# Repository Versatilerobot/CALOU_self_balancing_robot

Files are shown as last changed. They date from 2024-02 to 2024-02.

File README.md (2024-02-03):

# CALOU_self_balancing_robot
CALOU is an open source two-wheels inverted pendulum controlled by Bluetooth through a smartphone.

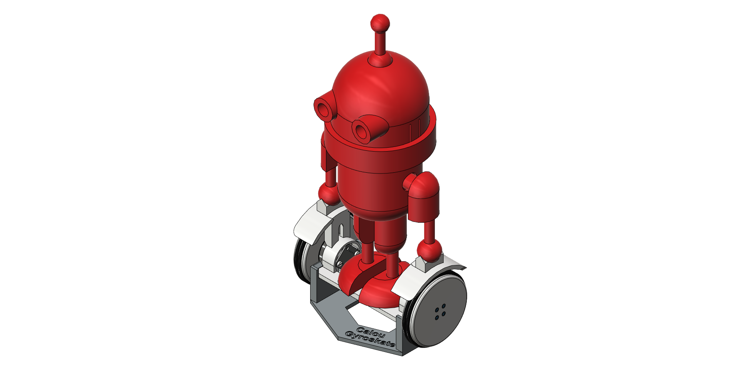
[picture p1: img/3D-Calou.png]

It is a personal project entirely 3D print and powered by two RC Brushless BR2804-100T Gimbal Motor and a 2-axis Brushless Gimbal Controller BGC3.1 MOSFET card in a close loop with angle magnetic encoders. Those parts need some modification &/o adaptation to be assembled. The Controller with the IMU and Bluetooth module HC-05 are located into the head while the Body holds in the center a 500mA – 11.1V – 30C LiPo battery with a switch. The arms and legs of the robot serve as wire guide for motors and encoders.

The program was adapted from an application example of [SimpleFOCproject](https://github.com/simplefoc) : Arduino library implementing a Field Oriented Control (FOC) algorithm for BLDC and Stepper motors: [Arduino-FOC-balancer](https://github.com/simplefoc/Arduino-FOC-balancer)

CALOU is the mascot of the French Robotic Association [Caliban](https://www.facebook.com/AssoCaliban)

It can be controlled through a smartphone by using a remote Bluetooth app and simple commands.   
I hope you will enjoy building this robot and have fun seeing it moving and stabilize and blinking its antenna.

# Assembly Instruction Manual

Assembly instructions have been written in English and French with illustrations to help you in the process step-by-step, making it easier for users to understand and follow:  
[CALOU - self-balancing robot_EN](/CALOU%20-%20self-balancing%20robot_EN.pdf)  
[CALOU - robot en gyroskate_FR](/CALOU%20-%20robot%20en%20gyroskate_FR.pdf)  

The main chapters are:  
Mechanical parts manufacturing; Electronic adaptations and wiring; The assembly steps of the robot; The programming, setting and tests; The starting procedure

A bill of material is also included: [BOM CALOU-GYROSKATE](/BOM%20CALOU-GYROSKATE.pdf)  
And all the STL files for the 3D printing: [3D_STL](/3D_STL)

As a reminder, it is given as is. The author gives no warranty and accepts no responsibility or liability for the accuracy or completeness of the information and materials contained in these instruction manuals.  

# CALOU on YouTube
[CALOU demo](https://youtu.be/TESaMDyrZCY?si=MoILjAsdVkf6BUT1)

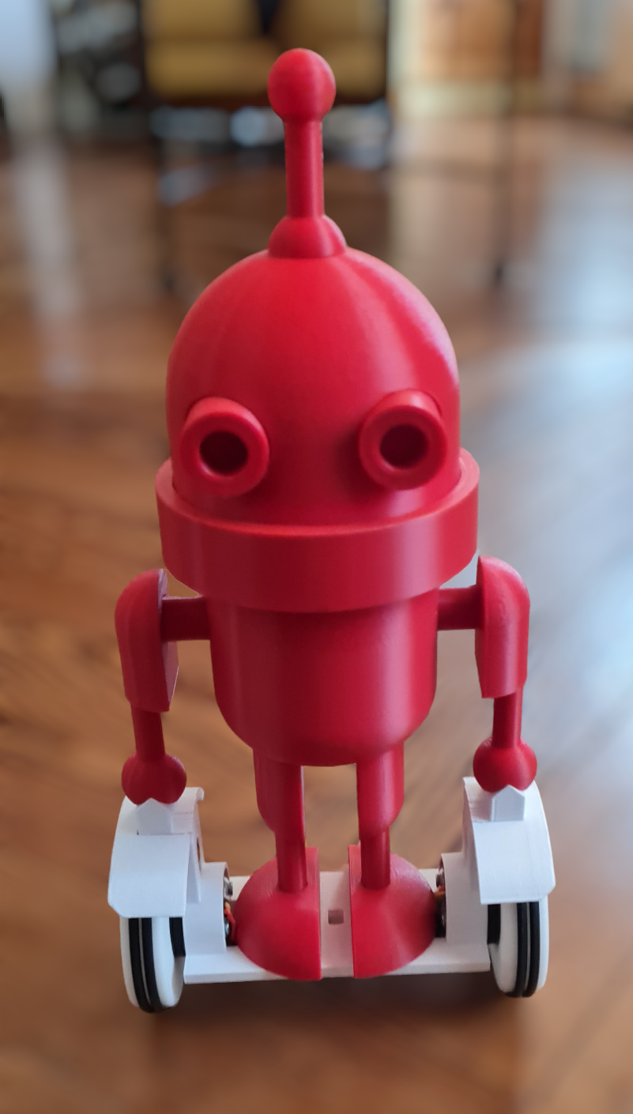
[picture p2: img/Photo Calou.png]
[](https://youtu.be/TESaMDyrZCY?si=MoILjAsdVkf6BUT1)

# Presentation - Apérobot 0x92 - 13th Dec 2023
[Apérobot 0x92 : Guy nous présente CALOU](https://youtu.be/fIwBQCcEI_Y?si=7qKZwHnpSAFOepEM)

Apérobot 0x92 : Guy nous présente CALOU (https://youtu.be/fIwBQCcEI_Y?si=7qKZwHnpSAFOepEM)

# Author

Guy FEUILLOLEY
https://www.facebook.com/versat.ilerobot

# MIT License
Permission is hereby granted, free of charge, to any person obtaining a copy of this software and associated documentation files (the "Software"), to deal in the Software without restriction, including without limitation the rights to use, copy, modify, merge, publish, distribute, sublicense, and/or sell copies of the Software, and to permit persons to whom the Software is furnished to do so, subject to the following conditions:

The above copyright notice and this permission notice shall be included in all copies or substantial portions of the Software.

THE SOFTWARE IS PROVIDED "AS IS", WITHOUT WARRANTY OF ANY KIND, EXPRESS OR
IMPLIED, INCLUDING BUT NOT LIMITED TO THE WARRANTIES OF MERCHANTABILITY, FITNESS FOR A PARTICULAR PURPOSE AND NONINFRINGEMENT. IN NO EVENT SHALL THE
AUTHORS OR COPYRIGHT HOLDERS BE LIABLE FOR ANY CLAIM, DAMAGES OR OTHER LIABILITY, WHETHER IN AN ACTION OF CONTRACT, TORT OR OTHERWISE, ARISING FROM, OUT OF OR IN CONNECTION WITH THE SOFTWARE OR THE USE OR OTHER DEALINGS IN THE SOFTWARE.

# Copyright
Copyright (c) 2024 Versatilerobot

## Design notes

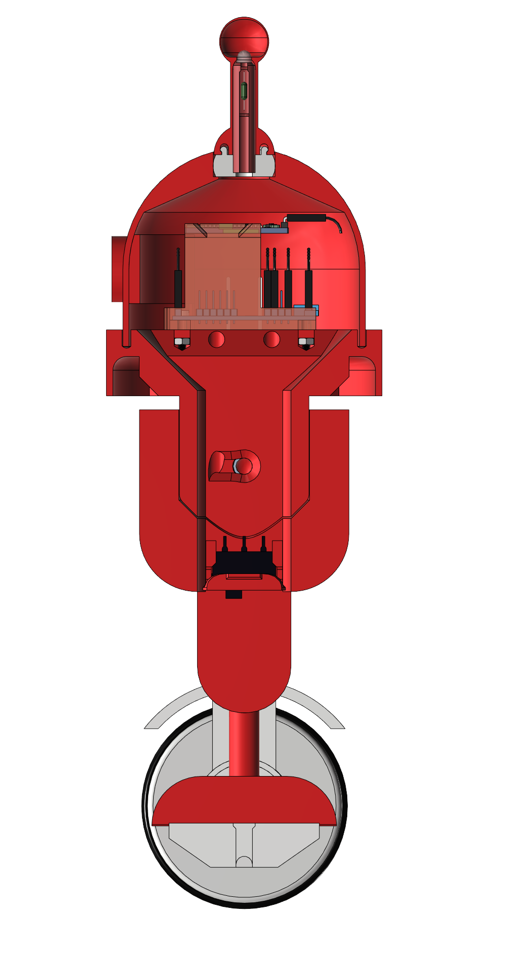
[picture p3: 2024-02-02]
img/CoupeProfil-Calou.png

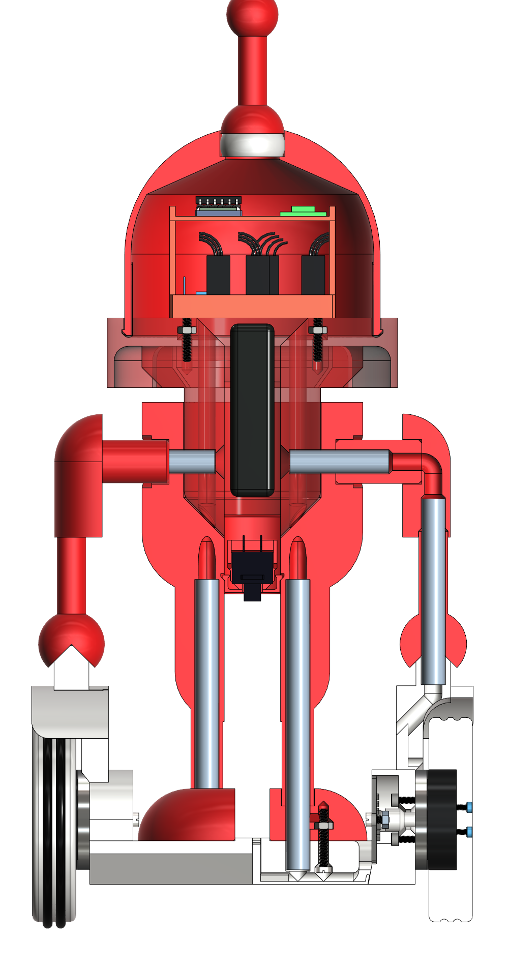
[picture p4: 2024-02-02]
img/CoupeFace-Calou.png

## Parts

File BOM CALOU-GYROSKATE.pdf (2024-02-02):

GF | BOM CALOU-GYROSKATE.xlsx | 02/02/2024

Electronic
componants

Price Per
Parcell €

Quantity
per Parcell

Quantity
needed

Price per
Unit €

Price per
Kit €
| | | | | | Notes | Examples
Moteurs 2804 100KV | 19,34 | 2 | 2 | 9,67 | 19,34 | Moteurs brushless de nacelle de drones | 2pcs/lot RC Brushless Gimbal Motor 2804 100KV For Gopro CNC Digital Camera (https://fr.aliexpress.com/item/32960476136.html)
Contrôleur de cardan sans balais à 2
axes, avec capteur gyro 6050 | 14,73 | 1 | 1 | 14,73 | 14,73 | BGC 3.1 MOS Courant de crête: 10A (à flasher avec bootloader
| | | | | | arduino) - Taille: 5*5cm | 2-axis BGC 3.1 Brushless Gimbal Controller/PTZ Controller motor Driver with 6050
| | | | | | | Sensor for FPV Multirotor (https://fr.aliexpress.com/item/32458535720.html)
Module Capteur d'Angle Magnétique | 1,23 | 1 | 2 | 1,23 | 2,46 | AS5600 - 12 Bits - avec aimant rond 4mm (Voir explication des
| | | | | | modifications à apporter au module 3,3V pour fonctionner en 5V) | TZT AS5600 magnetic encoder angle measurement sensor module 12bit high precision
| | | | | | | For aduino (https://fr.aliexpress.com/item/4000963821667.html)
Module Bluetooth HC-05 | 3,32 | 1 | 1 | 3,32 | 3,32 | Pour le contrôle par smartphone | HC-05 Master-Slave 6Pin, Integrated Bluetooth Serial Pass-Through Module, Wireless
| | | | | | | Serial for Arduino (https://fr.aliexpress.com/item/1005002082974256.html?curPageLogUid=oHJst9pOuJUH)
Accu LiPo 500mAh - 11,1v | 10,99 | 1 | 1 | 10,99 | 10,99 | Dimensions L x l x H = 58 x 32 x16 mm Poids avec câbles = 45g
| | | | | | Fiche d'équilibrage système = XH Fiche de courant système = BEC | Accu LiPo Extron X2 500 - 11,1v (30C - 60C) - Extron (https://www.miniplanes.fr/accu-lipo-extron-x2-500-111v-30c-60c-extron-x6403-p-508804.html)
Super Bright White LED | 0,49 | 1 | 1 | 0,49 | 0,49 | 5mm Super Bright White LED - 3 to 3,2V 20mA | Clear DIP LED Straw Hat (https://www.aliexpress.com/item/1005004635288313.html?curPageLogUid=oHyn5ukkpp4J)
Resistor | 0,12 | 1 | 1 | 0,12 | 0,12 | 1/4W 100Ω (100R) 1% | 100PCS 1/4W 100Ω 1% Metal Film Resistor (https://www.aliexpress.com/item/1005004525936064.html?curPageLogUid=Or2YflaCUnfN)
Extensions de Câble Servos 50cm | 10,99 | 10 | 6 | 1,10 | 6,59 | 3Pin - JR Style - Mâle à Femelle - Câble 22AWG | 10 pcs 50 cm JR Style Servo Extension Câbles (https://www.amazon.fr/dp/B08727C78V?ref=ppx_yo2ov_dt_b_product_details&th=1)
ON-OFF Rocker Switch | 5,09 | 10 | 1 | 0,51 | 0,51 | Black 6Pin ON-OFF - 10A 125V | SPST ON OFF Rocker Position Switch 21*15mm (https://www.aliexpress.com/item/1005006124139215.html)
10cm F to F jumper wires | 0,71 | 1 | 1 | 0,71 | 0,71 | 2.54mm Dupont Line 10cm 40Pin | Female Jumper Wire Dupont Cable DIY KIT (https://www.aliexpress.com/item/32481623557.html?curPageLogUid=Ydw5XZJNEJ00)
1x40 breakable Pin Header | 0,69 | 10 | 1 | 0,07 | 0,07 | Single Row Male 2.54mm Breakable Pin Header Connector Strip | 1x40 Single Row Male 2.54mm Breakable Pin Header Connector Strip (https://www.aliexpress.com/item/4000857385112.html?curPageLogUid=hJ3DWje0BWu6)
Tubes 100mm | 15,59 | 10 | 4 | 1,56 | 6,24 | Tube Droit 8x6mm - Aluminum | 10 Pièces en Aluminium Tube (https://www.amazon.fr/dp/B0BQGZ86W7?psc=1&ref=ppx_yo2ov_dt_b_product_details)
Joints Toriques 75mm | 11,25 | 5 | 4 | 2,25 | 9,00 | 75x68x3,5mm - Nitrile Caoutchouc | Nitrile Caoutchouc Joints Toriques 75mm OD 68mm ID 3.5mm (https://www.amazon.fr/dp/B07JYFP3N5?ref=ppx_yo2ov_dt_b_product_details&th=1)
Vis M2.5x8mm | 5,5 | 50 | 8 | 0,11 | 0,88 | Tête cylindrique - DIN 912 - Acier Inoxydable A2 | 50 Boulons - Tête cylindrique - M2.5x8mm (https://www.amazon.fr/dp/B072MJTMK6?ref=ppx_yo2ov_dt_b_product_details&th=1)
Vis M3x20mm | 13,88 | 20 | 6 | 0,69 | 4,16 | acier inoxydable 304 - tête cylindrique fendue | 20 boulons à tête cylindrique fendue M3 x 20 mm (https://www.amazon.fr/sourcing-map-inoxydable-boulons-cylindrique/dp/B0C143GYQM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)
Vis M3x8mm | 8,78 | 20 | 4 | 0,44 | 1,76 | Tête fraisée - DIN 965 Phillips | 20 vis à tête fraisée M3 x 8 mm en acier inoxydable (https://www.amazon.fr/SECCARO-frais%C3%A9e-inoxydable-Phillips-Filetage/dp/B0CKTK37C4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)
Écrou Hexagonal M3 | 6,99 | 40 | 10 | 0,17 | 1,75 | Acier Inoxydable | 40 Pièces M3 Écrou en Acier Inoxydable (https://www.amazon.fr/Pi%C3%A8ces-Blocage-Inoxydable-Hexagonal-%C3%89crous/dp/B0BDDPQJ9L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)
| | | | | 83,12
3D parts raw material | Price
| €/Kg | Weight
| | g | Quantity
| | | needed | Price Per
| | | | Unit € | Price per
| | | | | kit € | Notes
| | | | | | A titre indicatif seulement - Imprimante Flsun FQQ Pro | Examples
Antenne | 25 | 4 | 1 | 0,10 | 0,10 | 1,25m PLA Rouge 0h24 min | SUNLU Meta Filament PLA 1,75 mm ROUGE (https://www.amazon.fr/dp/B0B24Y84LN/ref=twister_B0B87C7YH4?_encoding=UTF8&th=1)
AvBras | 25 | 4 | 2 | 0,10 | 0,20 | 2,98m PLA Rouge 0h32 min
AxeAimant | 25 | 1 | 2 | 0,03 | 0,05 | 0,23m PLA Rouge 0h16 min
Base | 25 | 38 | 1 | 0,95 | 0,95 | 12,9m PLA Gris 2h47 min | SUNLU Meta Filament PLA 1,75 mm GRIS (https://www.amazon.fr/dp/B0B24W9WLL/ref=twister_B0B87C7YH4?_encoding=UTF8&psc=1)
Bras | 25 | 4 | 2 | 0,10 | 0,20 | 2,92m PLA Rouge 0h48 min
CacheFils | 25 | 1 | 1 | 0,03 | 0,03 | 0,45m PLA Blanc 0h10 min
CaleLedAntenne | 25 | 1 | 1 | 0,03 | 0,03 | 0,46m PLA Rouge 0h16 min
CorpsBas-V2 | 25 | 121 | 1 | 3,03 | 3,03 | 40,56m PLA Rouge 7h10 min
CorpsHaut | 25 | 111 | 1 | 2,78 | 2,78 | 37,16m PLA Rouge 6h34 min
Epaule | 25 | 11 | 2 | 0,28 | 0,55 | 3,57m PLA Rouge 1h22 min
GardeBoue | 25 | 7 | 2 | 0,18 | 0,35 | 2,46m PLA Blanc 0h30 min
GyroskateCorps | 25 | 65 | 1 | 1,63 | 1,63 | 21,71m PLA Blanc 4h02 min
JointLed | 25 | 3 | 1 | 0,08 | 0,08 | 0,89m TPU Blanc 0h10 min | ERYONE TPU Filament 1.75mm (https://www.amazon.fr/ERYONE-Filament-1-75mm-Drucker-0-05mm/dp/B07WDF31WP?hvadid=411298501561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)
Pied | 25 | 14 | 2 | 0,35 | 0,70 | 9,44m PLA Rouge 0h48 min
Roue | 25 | 27 | 2 | 0,68 | 1,35 | 17,94m TPU Blanc 3h04 min | ERYONE TPU Filament 1.75mm (https://www.amazon.fr/ERYONE-Filament-1-75mm-Drucker-0-05mm/dp/B07WDF31WP?hvadid=411298501561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)
SupportBGCboard | 25 | 8 | 1 | 0,20 | 0,20 | 2,83m PLA Rouge 0h58 min
SupportIMU&BLE | 25 | 3 | 1 | 0,08 | 0,08 | 1,00m PLA Rouge 0h17 min
Tête | 25 | 57 | 1 | 1,43 | 1,43 | 19,00m PLA Rouge 3h48 min
TrappeSwitch-V2 | 25 | 3 | 1 | 0,08 | 0,08 | 0,86m PLA Rouge 0h17 min
Yeux | 25 | 21 | 1 | 0,53 | 0,53 | 7,00m PLA Rouge 1h27 min
| | 504 | 27 | | 14,30
3D parts printing electricity | Price
| €/kWh | 3D printer
| | Power W | Quantity
| | | needed h | 3D printer
| | | | price kWh | Price per
| | | | | kit € | Notes
| | | | | | A titre indicatif seulement - Imprimante Flsun FQQ Pro
| 0,21 | 150 | 35,7 | 0,03 | 1,12
Total | | | | | 98,54

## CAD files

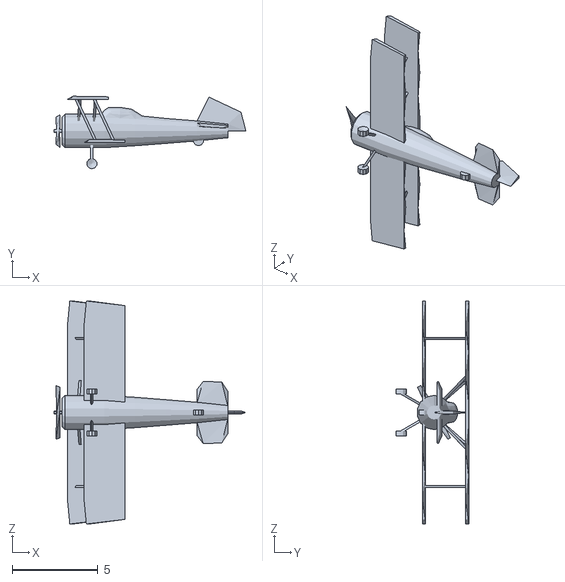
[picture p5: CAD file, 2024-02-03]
Calou_Gyroskate/src/MPU6050/Examples/MPU6050_DMP6_using_DMP_V6.12/MPUplane/data/biplane.obj
11.2 x 4.23 x 13.0

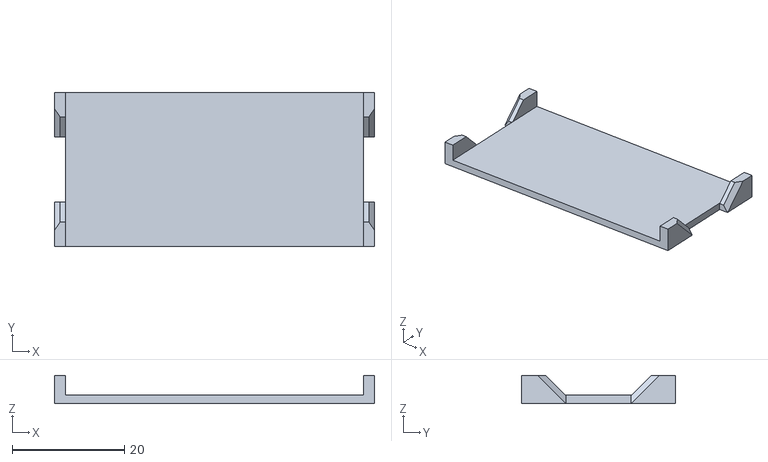
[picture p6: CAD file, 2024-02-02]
3D_STL/SupportIMU&BLE.stl
57.0 x 27.5 x 5.00

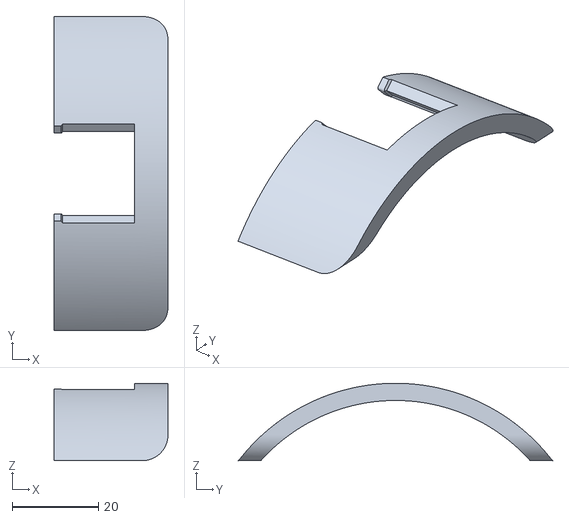
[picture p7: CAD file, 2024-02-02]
3D_STL/GardeBoue.stl
26.5 x 73.0 x 18.0

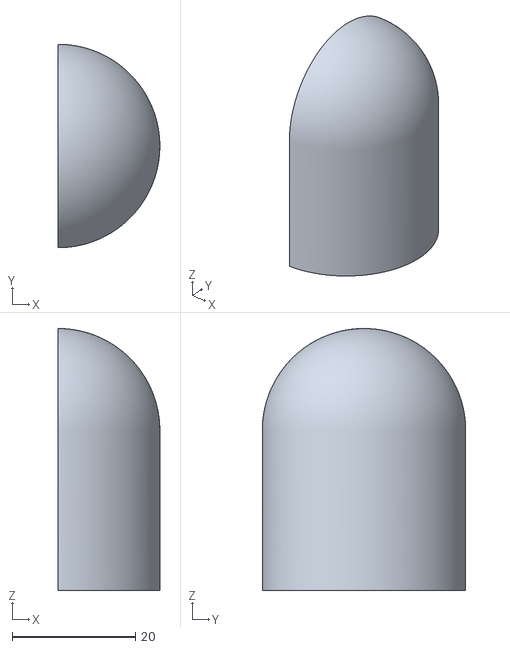
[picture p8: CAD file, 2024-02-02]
3D_STL/Epaule.stl
16.5 x 33.0 x 42.5

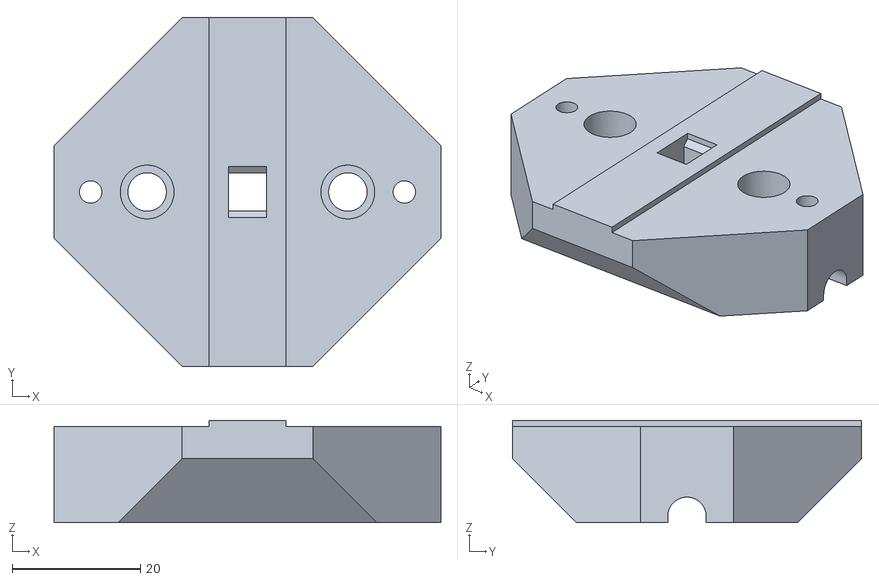
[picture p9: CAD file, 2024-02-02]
3D_STL/FootSpacer.stl
60.4 x 54.5 x 16.0

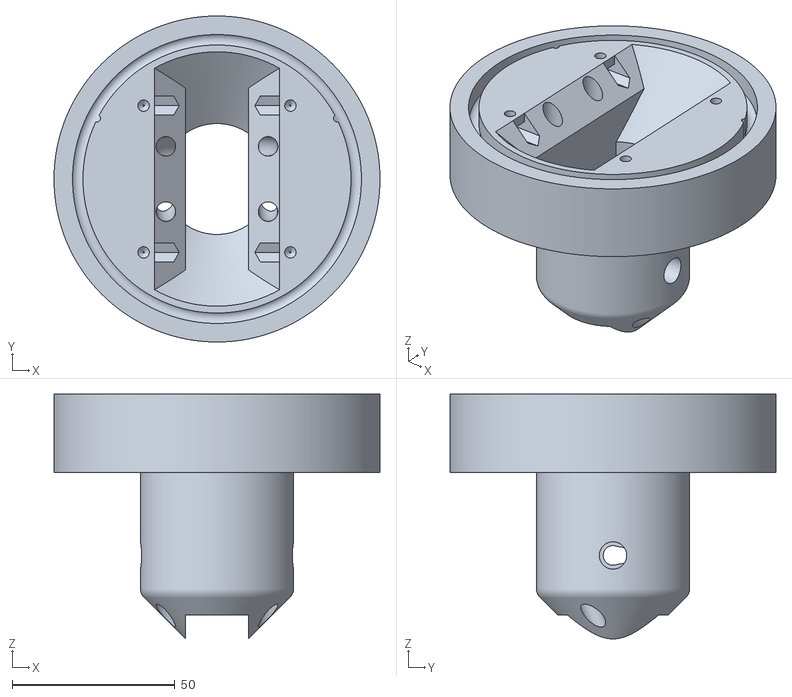
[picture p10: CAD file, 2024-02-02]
3D_STL/CorpsHaut.stl
100.0 x 100.0 x 75.1

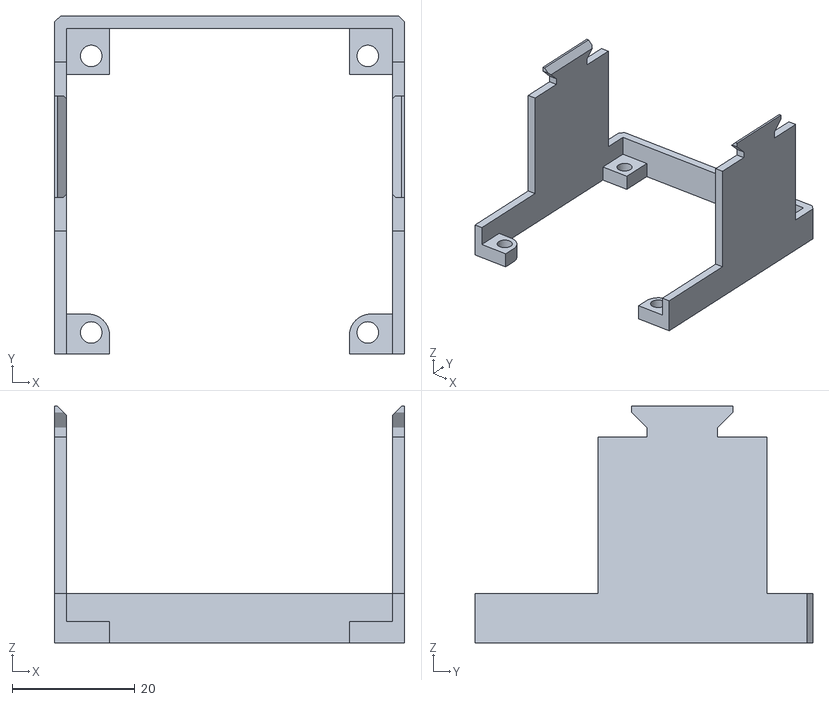
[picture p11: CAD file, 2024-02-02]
3D_STL/SupportBGCboard.stl
57.0 x 55.0 x 38.5

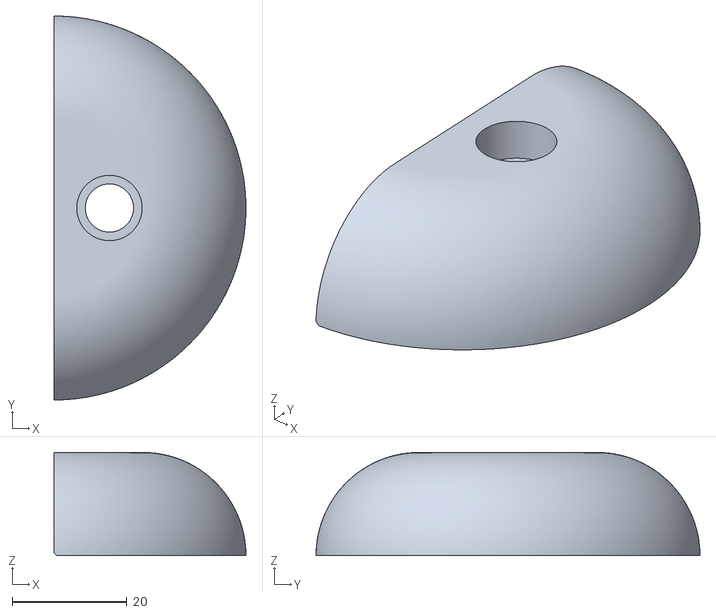
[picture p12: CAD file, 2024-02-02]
3D_STL/Pied.stl
33.5 x 67.0 x 18.0

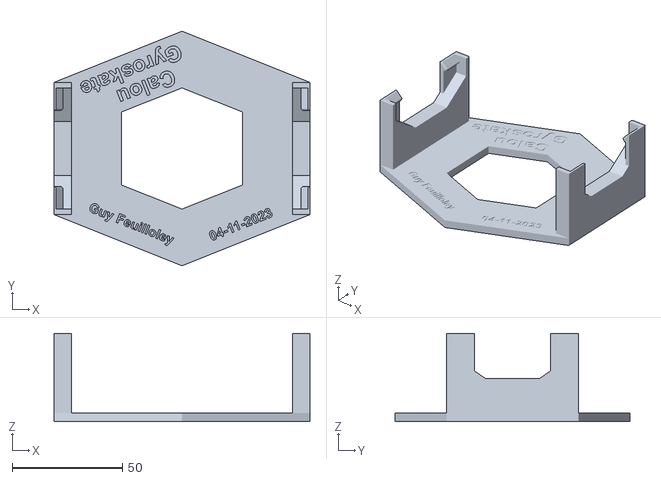
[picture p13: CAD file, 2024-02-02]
3D_STL/Base.stl
116.1 x 106.4 x 40.0

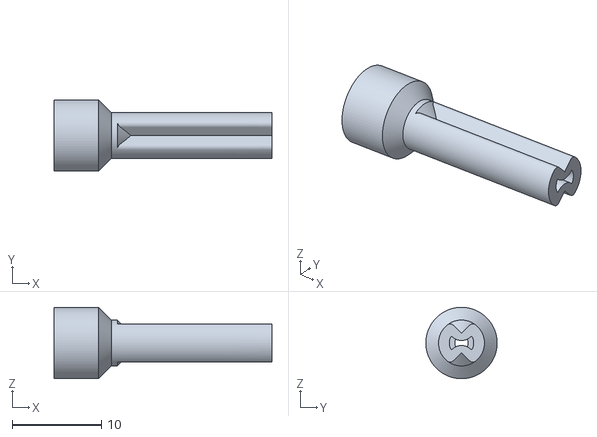
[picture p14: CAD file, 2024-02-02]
3D_STL/AxeAimant.stl
24.4 x 8.00 x 8.00

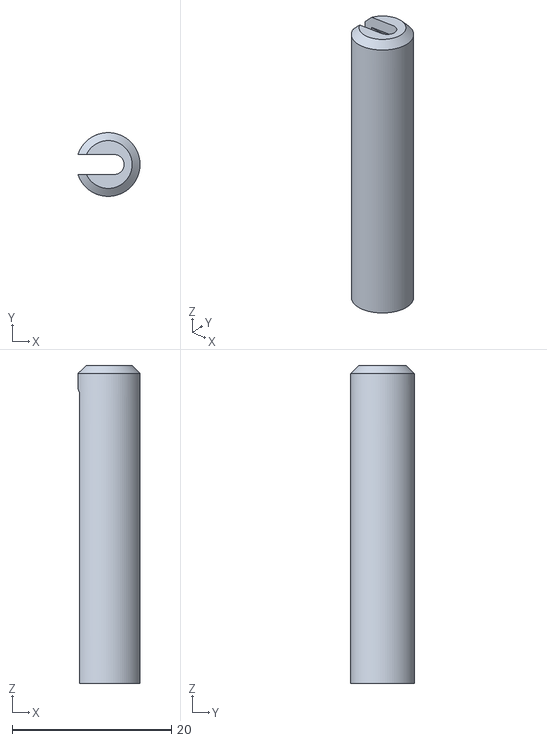
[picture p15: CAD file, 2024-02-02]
3D_STL/CaleLedAntenne.stl
7.80 x 8.00 x 39.9

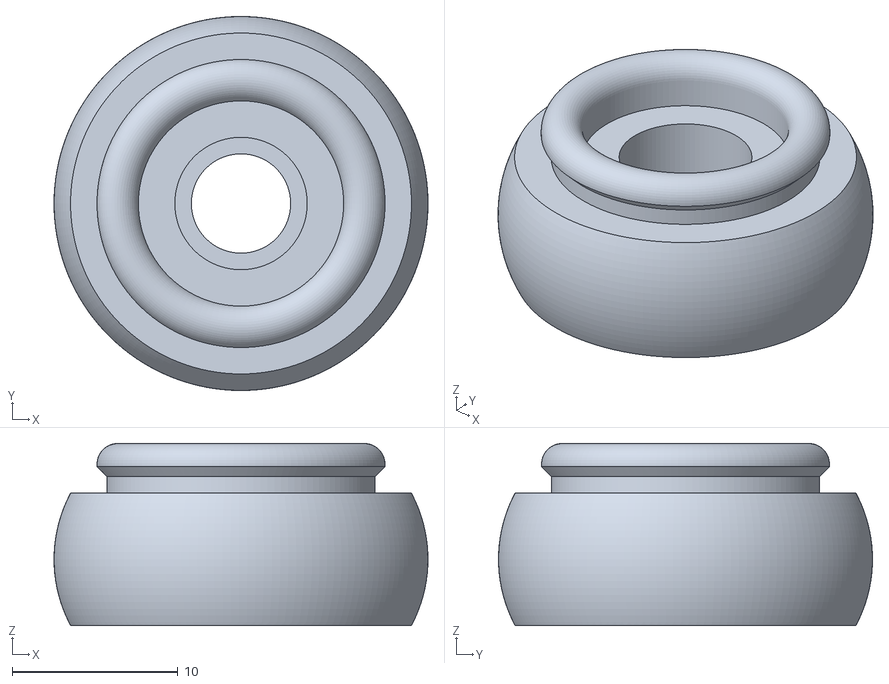
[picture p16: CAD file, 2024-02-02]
3D_STL/JointLed.stl
22.6 x 22.6 x 11.0

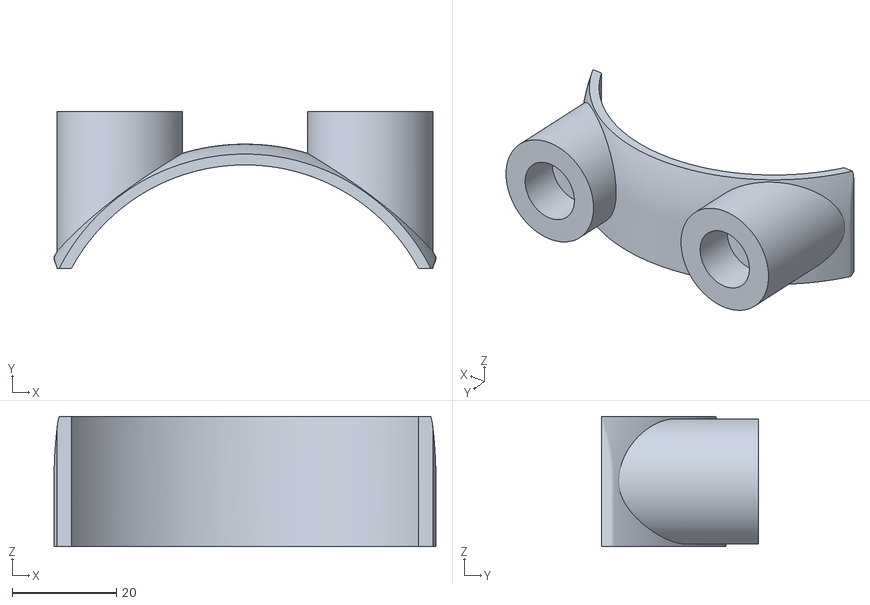
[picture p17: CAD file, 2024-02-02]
3D_STL/Yeux.stl
73.2 x 30.0 x 25.0

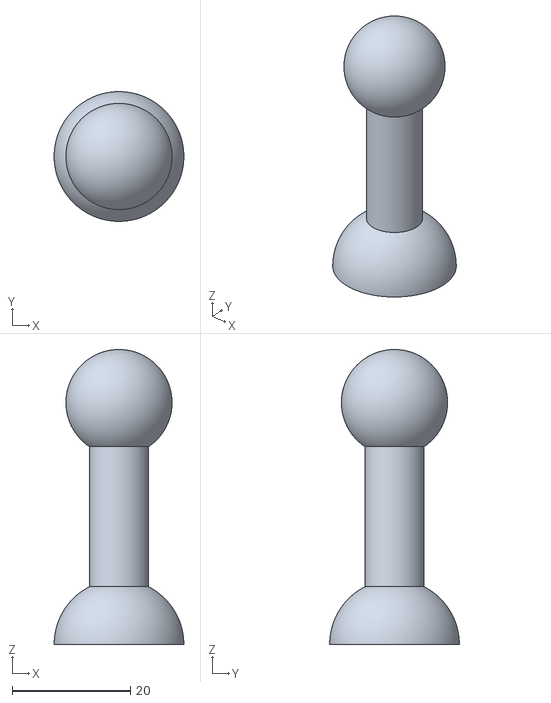
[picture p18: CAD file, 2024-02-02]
3D_STL/Antenne.stl
22.0 x 22.0 x 50.0

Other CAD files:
3D_STL/TrappeSwitch-V3.stl
3D_STL/AvBras.stl
3D_STL/CacheFils.stl
3D_STL/Roue.stl
3D_STL/Bras.stl
3D_STL/GyroskateCorps.stl
3D_STL/TrappeSwitch-V2.stl
3D_STL/Tête.stl

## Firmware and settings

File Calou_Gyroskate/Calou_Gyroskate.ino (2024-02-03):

/* Calou_Gyroskate
 * This is a sketch for a two wheel balancing robot done for a BGC 3.1 Brushless Gimbal Controller with gimbal BLDC motors and SimpleFOClibrary. 
 * It was derived from the application example done for a STM32 Nucleo-64 board you can find on the github "SimpleFOCproject": Arduino SimpleFOCBalancer
 https://docs.simplefoc.com
 https://github.com/simplefoc/Arduino-FOC-balancer
 */

#include "imu_helpers.h"
#include "src/SimpleFOC.h" // ver. 1.61

//// create motor and sensor instances
//BLDCMotor motorL = BLDCMotor(3, 5, 6, 7); // pins + pole pairs
//MagneticSensorAnalog sensorL = MagneticSensorAnalog(A0, 14, 1020);
//
//BLDCMotor motorR = BLDCMotor(9, 10, 11, 7); // pins + pole pairs
//MagneticSensorAnalog sensorR = MagneticSensorAnalog(A1, 14, 1020);

//magnetic sensor instance
MagneticSensorAnalog sensorL = MagneticSensorAnalog(A1, 14, 1020);
MagneticSensorAnalog sensorR = MagneticSensorAnalog(A0, 14, 1020);
// motor instance
BLDCMotor motorL = BLDCMotor(9, 10, 11, 7); // pins + pole pairs
BLDCMotor motorR = BLDCMotor(3, 5, 6, 7); // pins + pole pairs

// control algorithm parameters
// stabilisation pid
PIDController pid_stb{.P = 50, .I = 90, .D = 2, .ramp = 100000, .limit = 10};
// velocity pid
PIDController pid_vel{.P = 0.015, .I = 0.01, .D = 0, .ramp = 2000, .limit = _PI / 10};
// velocity control filtering
LowPassFilter lpf_pitch_cmd{.Tf = 0.35};
// low pass filters for user commands - throttle and steering
LowPassFilter lpf_throttle{.Tf = 0.4};
LowPassFilter lpf_steering{.Tf = 0.01};

// Bluetooth variables
int state = 1;           // stabilization enabling
float steering = 0;
float throttle = 0;
float max_throttle = 20; // 20 rad/s
float max_steering = 1;  // 1 V
float MaxAngle = PI/8;   // dead angle activation limit 
char Incoming_value = 0; // Variable for storing serial value

// constants won't change. Used here to set a pin number :
const int ledPin =  A3;             // the pin of the LED antenna
int ledState = LOW;                 // ledState used to set the LED
unsigned long previousMillis = 0;   // will store last time LED was updated
long interval = 1000;               // interval at which to blink (milliseconds)

void setup() {
  // use monitoring with Serial for motor init
  // monitoring port
  Serial.begin(9600);
  // set the digital pin as output:
  pinMode(ledPin, OUTPUT);  
  delay(1000);
  // imu init and configure
  if ( !initIMU() ) {
    Serial.println(F("IMU connection problem... Disabling!"));
    return;
  }
  delay(1000);
  
  // initialise magnetic sensor hardware
  sensorL.init();
  sensorR.init();                                             
  // link the motor to the sensor
  motorL.linkSensor(&sensorL);
  motorR.linkSensor(&sensorR);
  // power supply voltage
  // default 12V
  motorL.voltage_power_supply = 11;
  motorR.voltage_power_supply = 11;
  // set motion control loop to be used  
  motorL.controller = ControlType::voltage;
  motorR.controller = ControlType::voltage;
  // choose FOC modulation (optional)  
  motorL.foc_modulation = FOCModulationType::SpaceVectorPWM;
  motorR.foc_modulation = FOCModulationType::SpaceVectorPWM;
  // initialize motor 
  motorL.init();
  motorR.init();
  // align encoder and start FOC
  // before upload this sketch please look at the instructions for find sensor
  // offset and direction of the motors corresponding to your robot (sketch: find_sensor_offset_and_direction.ino)                                                 
  motorL.initFOC(); // must be updated with your values e.g: motorL.initFOC(6.0520,CCW);
  motorR.initFOC();  // must be updated with your values e.g: motorR.initFOC(0.1287,CW);                                   
  delay(2000);
  Serial.println(F("Balancing robot ready!"));
}

void loop() {
  
  // antenna blink update
  BlinkLed();
  
  // main FOC algorithm function
  motorL.loopFOC();
  motorR.loopFOC();

  // motion control function
  motorL.move();
  motorR.move();

  if (!state) { // if balancer disabled
    motorL.target = 0;
    motorR.target = 0;
  } else if ( hasDataIMU() ) { // when IMU has received the package
    // read pitch from the IMU
    float pitch = getPitchIMU();
    //Serial.println(pitch);
    if (pitch < MaxAngle && pitch > -MaxAngle){
    pitch = pitch - PI/180; //offset of the verticale position link to the sensor mounting (optional)
    // calculate the target angle for throttle control
    float target_pitch = lpf_pitch_cmd(pid_vel((motorL.shaft_velocity + motorR.shaft_velocity) / 2 - lpf_throttle(throttle)));  
    // calculate the target voltage
    float voltage_control = pid_stb(target_pitch - pitch);
    // filter steering
    float steering_adj = lpf_steering(steering);
    // set the target voltage value
    motorL.target = voltage_control + steering_adj;
    motorR.target = voltage_control - steering_adj;
  }
  else {
    throttle = 0;
    steering = 0;
  }
}

// read the user command from bluetooth
  Bluetooth();
}

void BlinkLed() {

  unsigned long currentMillis = millis()/32; // timer was changed by the SimpleFOC library

  if (currentMillis - previousMillis >= interval) {
    // save the last time you blinked the LED
    previousMillis = currentMillis;
    // if the LED is off turn it on and vice-versa:
    if (ledState == LOW) {
      ledState = HIGH;
    } else {
      ledState = LOW;
    }
    // set the LED with the ledState of the variable:
    digitalWrite(ledPin, ledState);
  }
}

void Bluetooth() {
  if (Serial.available()> 0){  
  Incoming_value = Serial.read();     
  if(Incoming_value != '\n')
  {
    if (Incoming_value == '1') {
      // stabilization enabled
      steering = 0;
      throttle = 0;
      state = 1;
    } else if (Incoming_value == '0') {
      // stabilization disabled
      steering = 0;
      throttle = 0;
      state = 0;
    } else if (Incoming_value == 'A') {
      if (throttle < max_throttle) throttle = throttle + 2; // move forward - send several time for accelerate
    } else if (Incoming_value == 'R') {
      if (throttle > - max_throttle) throttle = throttle - 2; // move backward - send several time for accelerate
    } else if (Incoming_value == 'G') {
      if (steering > - max_steering) steering = steering - 0.05; // turn left - send several time for shorting the radius   
    } else if (Incoming_value == 'D') {
      if (steering < max_steering) steering = steering + 0.05; // turn right - send several time for shorting the radius
    } else if (Incoming_value == 'L') {
      steering = 0; // stop steering
    } else if (Incoming_value == 'S'){
      // stop moving
      steering = 0;
      throttle = 0;
      }
    }
  }
}

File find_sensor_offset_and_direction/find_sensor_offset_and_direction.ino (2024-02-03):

/* find_sensor_offset_and_direction
 https://docs.simplefoc.com

 * Simple example intended to help users find the zero offset and natural direction of the sensor.  
 * These values can further be used to avoid motor and sensor alignment procedure. 
 * motor.initFOC(zero_offset, sensor_direction);
 * This will only work for abosolute value sensors - magnetic sensors. 
 * Bypassing the alignment procedure is not possible for the encoders and for the current implementation of the Hall sensors. 
 * 
 */
#include "src/SimpleFOC.h" // ver. 1.6.1

MagneticSensorAnalog sensorL = MagneticSensorAnalog(A1, 14, 1020);
MagneticSensorAnalog sensorR = MagneticSensorAnalog(A0, 14, 1020);

// BLDC motor instance
BLDCMotor motorL = BLDCMotor(9, 10, 11, 7); // pins + pole pairs
BLDCMotor motorR = BLDCMotor(3, 5, 6, 7); // pins + pole pairs

void setup() {

  // initialise magnetic sensor hardware
  sensorL.init();
  sensorR.init();
  // link the motor to the sensor
  motorL.linkSensor(&sensorL);
  motorR.linkSensor(&sensorR);
  // power supply voltage
  // default 12V
  motorL.voltage_power_supply = 12;
  motorR.voltage_power_supply = 12;
  // aligning voltage 
  motorL.voltage_sensor_align = 7;
  motorR.voltage_sensor_align = 7;
  // set motion control loop to be used
  motorL.controller = ControlType::voltage;
  motorR.controller = ControlType::voltage;
  // initialize motor
  motorL.init();
  motorR.init();  
  // align sensor and start FOC
  motorL.initFOC();
  motorR.initFOC();
  
  Serial.begin(9600);
  Serial.println("motorL");
  Serial.print("Offset: ");
  Serial.print(motorL.zero_electric_angle, 4);
  Serial.println(sensorL.natural_direction == 1 ? " Direction: CW" : " Direction: CCW"); 

  Serial.println("motorR");
  Serial.print("Offset: ");
  Serial.print(motorR.zero_electric_angle, 4);   
  Serial.println(sensorR.natural_direction == 1 ? " Direction: CW" : " Direction: CCW");  
  Serial.println("To use these values provide them to the robot sketch:");
  Serial.println("motorL.initFOC(offset, direction)");
  Serial.println("motorR.initFOC(offset, direction)");  
  _delay(1000);
  Serial.println("If motor are not moving the alignment procedure was not successfull!!");

}

void loop() {
    
  // main FOC algorithm function
  motorL.loopFOC();
  motorR.loopFOC();

  // motion control function
  motorL.move(2);
  motorR.move(2);
  
}
